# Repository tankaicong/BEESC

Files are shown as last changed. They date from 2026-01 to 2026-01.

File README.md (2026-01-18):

# Project BEESC

This is a custom ESC based on the VESC6 architecture that is planned to be pin compatible with the Bumblebee AUV5.0 vehicle.

## Current Design

2D View:

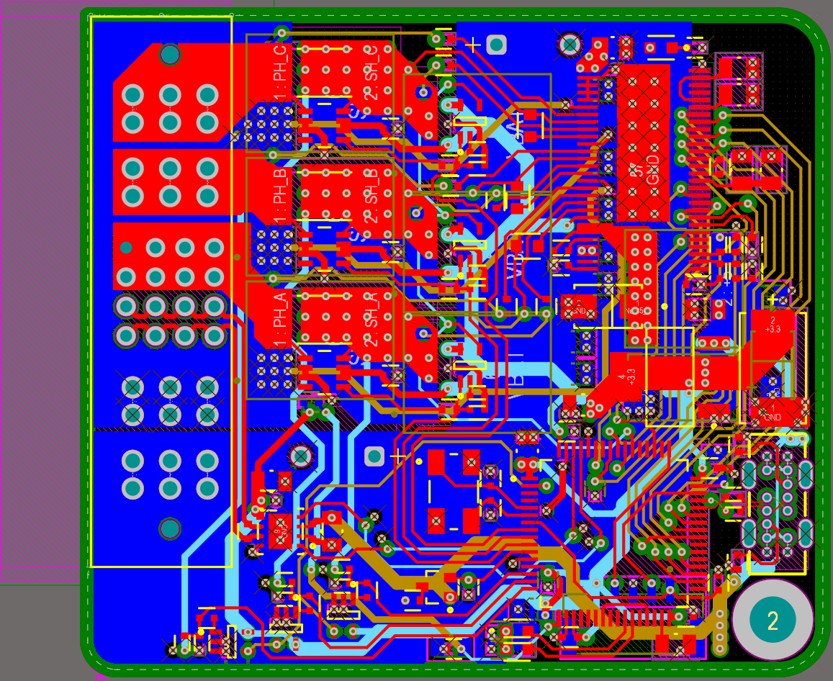
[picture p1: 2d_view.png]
2D View of PCB


3D View (Top):

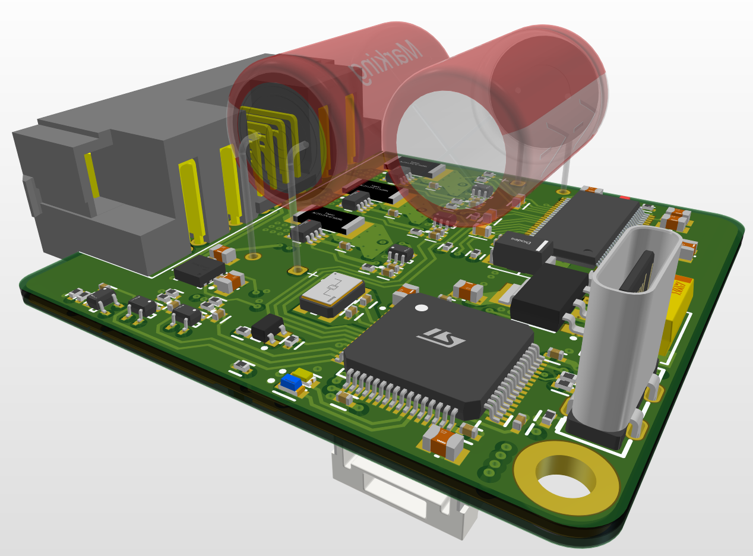
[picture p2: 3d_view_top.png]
3D top view of PCB


3D View (Bottom):

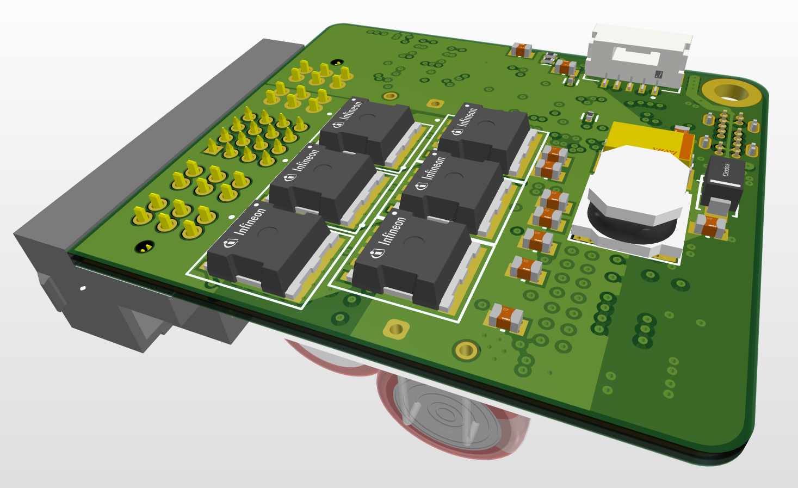
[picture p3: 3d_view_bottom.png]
3D Bottom View of PCB


6 layer used due to high density of components, stack-up used is the standard SIG-GND-SIG-SIG-GND-SIG, but top and bottom layers are more dedicated to power polygon pours and 4th layer is mainly 5V/3.3V power traces more than signal traces.

Rough layout process was:
1) Place the motor MOSFETs as close to the connectors as possible
2) Power pours just automatically falls into place
3) Routing MOSFET control/feedback signals to the driver IC
4) Routing MCU signals to the driver
5) Routing remaining feedback signals to MCU
5) Routing 5V/3.3V power

## Rationale

The main purpose for this is to shrink the ESCs down as much as possible. The current approach of using commercial ESCs are quite bulky and overkill, since they are usually rated for 12S, three times above our own battery sizes. Hence, it was thought that the smaller ESC should be feasible.

The other purpose is to try FOC control and eventually closed-loop control.

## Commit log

2025-12-14 add driver schematic
    [DRV8301.SchDoc, Project_BEESC.PrjPcb]
2025-12-15 feat: add local library with motor driver components
    [BEESC_footprints.PcbLib, BEESC_symbol.SchLib]
2025-12-15 feat: add drv8301 schematic
    [DRV8301.SchDoc, Project_BEESC.PrjPcb]
2025-12-16 chore: add dummy schdoc and pcbdoc
    [BEESC_footprints.PcbLib, BEESC_symbol.SchLib, BEESC_v1.PcbDoc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]
2025-12-17 feat: completed first draft of schematic
    [BEESC_footprints.PcbLib, BEESC_symbol.SchLib, CAN.SchDoc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]
2026-01-02 fix: modified CS amplifier
    [BEESC_symbol.SchLib, CAN.SchDoc, Power.SchDoc]
2026-01-02 chore: clean up schematic sheets (add borders, titles)
    [CAN.SchDoc, DRV8301.SchDoc, MCU.SchDoc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]
2026-01-03 feat: add main schematic
    [BEESC_symbol.SchLib, CAN.SchDoc, DRV8301.SchDoc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]
2026-01-03 fix: add GND to source of all low-side MOSFETs
    [Power.SchDoc]
2026-01-03 feat: initial layout for mosfet/power related components
2026-01-04 feat: add iniital high current power pours
    Considering switching to 6-layer board due to JLCPCB offer which makes it cheaper than 4-layer board.
    This likely does not affect placement but some power pours will end up in inner layers.
    [BEESC_symbol.SchLib, Power.SchDoc]
2026-01-05 fix: resolve duplicate GND net issue
    [MCU.SchDoc, Main.SchDoc, Power.SchDoc]
2026-01-06 feat: add DRV8301, route power pours and mosfet signals
    [Main.SchDoc, Project_BEESC.PrjPcb]
2026-01-06 fix: add inline 22R resistors to DP/DM lines
    [BEESC_symbol.SchLib, Main.SchDoc]
2026-01-07 fix: set VDD_SPI to 3.3V instead of 5V
    [DRV8301.SchDoc]
2026-01-07 feat: finsh routing all power side parts and preliminary layout of signal side parts
2026-01-08 fix: rotate bottom left bulk capacitor
    [Power.SchDoc]
2026-01-08 fix: add differential pair designation for USB signals
    [MCU.SchDoc, Main.SchDoc]
2026-01-08 feat: layout of all driver components, preliminary layout of MCU and its components, expand board height for more area
2026-01-09 [HW]: shrink to GH connector for SWD, remap current sense pins for easier routing
    [BEESC_symbol.SchLib, MCU.SchDoc, Main.SchDoc]
2026-01-09 [HW]: layout all components in board, route almost all signals except MCU to DRV8301 signals
    [BEESC_symbol.SchLib, Power.SchDoc]
2026-01-14 initial bb server commit
    [Project_BEESC.PrjPcb]
2026-01-16 [HW] minor polygon modifications
    [BEESC_v1.PcbDoc]
2026-01-16 initial 8 layer board design trying 8 layers to use inner plane as VBAT, since bottom layer is quite broken up by vias but inner power plane is also broken up just as badly, if not worst, from the ma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
    [BEESC_v1_L8.PcbDoc, Project_BEESC.PrjPcb]
2026-01-16 initial 8 layer board design trying 8 layers to use inner plane as VBAT, since bottom layer is quite broken up by vias but inner power plane is also broken up just as badly, if not worst, from the ma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
    [Project_BEESC.PrjPcb]
